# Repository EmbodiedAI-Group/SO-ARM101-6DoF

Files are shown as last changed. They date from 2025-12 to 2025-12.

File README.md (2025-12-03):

<div align="center">

   <h1>Standard Open SO-100 & SO-101 & SO-101-6DOF Arms</h1>
   <div style="display: flex; gap: 1rem; justify-content: center; align-items: center;" >
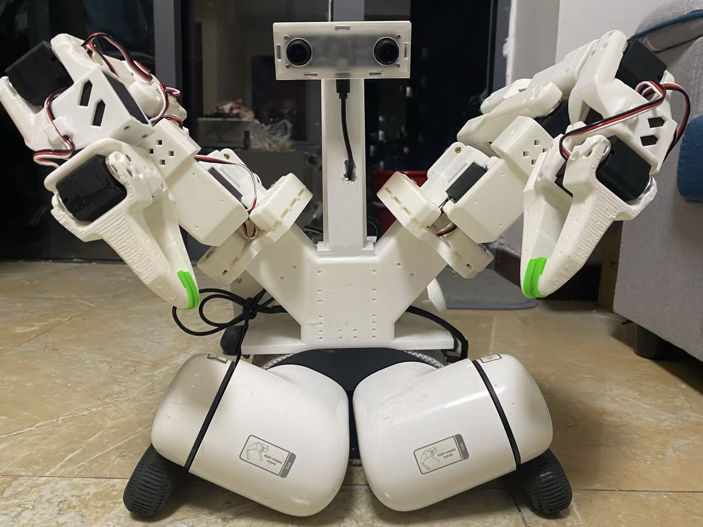
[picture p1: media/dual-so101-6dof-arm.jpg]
Dual SO-101 6dof follower arm DUAL SO-101 6DOF follower arm
   
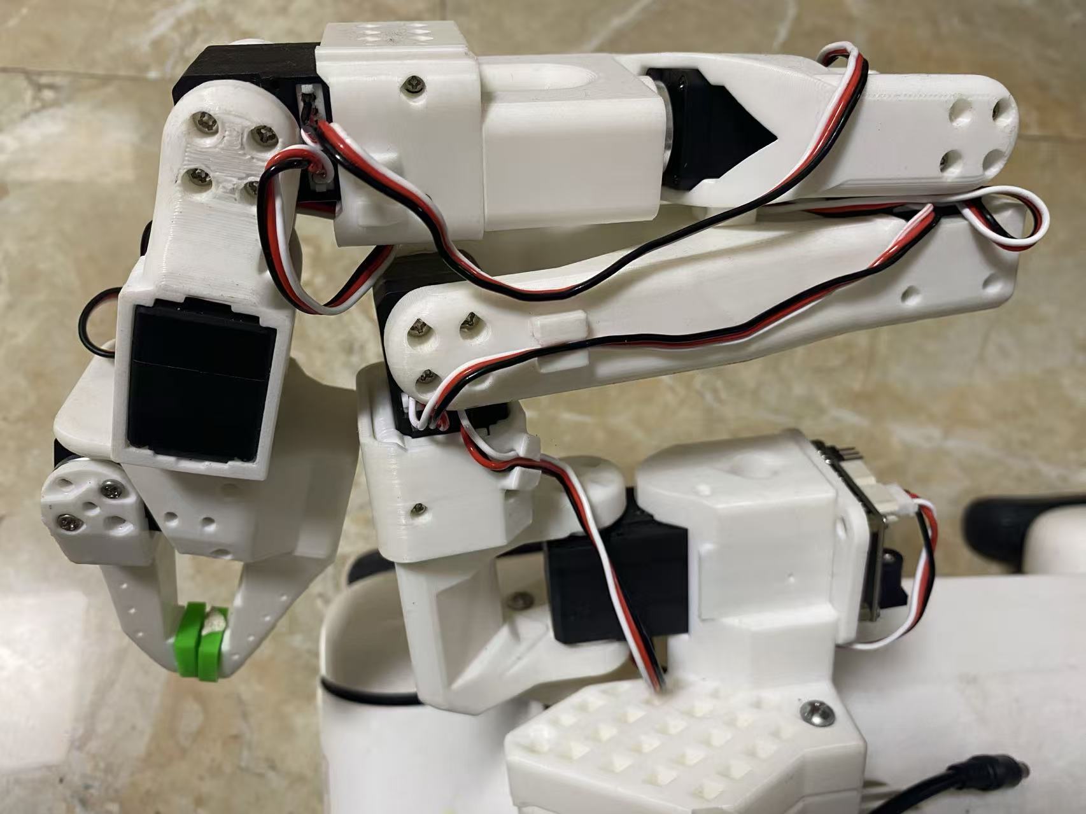
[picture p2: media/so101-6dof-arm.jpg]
SO-101 6dof follower arm SO-101 6DOF follower arm
   
   SO-101 follower arm
   SO-101 leader arm
</div>

<h2>
    <p>Build Your Own SO-101(-6DOF) Robot!</p>
</h2>

The SO‑101(-6DOF) is the next‑generation version of the SO‑100 robot arm, originally designed by the [RobotStudio](https://www.therobotstudio.com) in collaboration with [Hugging Face](https://huggingface.co/lerobot). It has improved wiring, is easier to assemble (no gear removal) and uses updated motors for the leader arm.

These arms are designed to work seamlessly with the open‑source 🤗 LeRobot library. Join our community on [Discord](https://discord.gg/ggrqhPTsMe) to collaborate on both hardware and software, and help make end‑to‑end AI for robotics more accessible.

</div>

### Documentation 📖
- For the SO‑101 docs, follow this page further.
- Here you can find the [SO‑100 docs](SO100.md) which is deprecated.

### Getting Your Own SO‑101 
You have two options:
- **Build it Yourself**
   - Source the components from the [Bill of Materials](#sourcing-parts).
   - 3D print the parts (or order the 3D printed parts), explained in [Printing the Parts](#printing-the-parts).
   - Follow our [Assembly Guide](https://huggingface.co/docs/lerobot/so101).
- **Buy a Kit**
   - Buy assembled arms or a parts kit from one of the vendors [here](#kits).
   - Optionally follow our [Assembly Guide](https://huggingface.co/docs/lerobot/so101).

### Setup with LeRobot 🤗
After sourcing all parts you can setup your SO-101(-6DOF) with LeRobot [tutorial](https://huggingface.co/docs/lerobot/so101). 

### Optional Hardware 🔧
This repository also includes a range of optional hardware designs such as a raised leader base and different camera mounts. Here you can explore the [full list](#optional-hardware).

## Kits

You can find all optional for SO-100/SO-101 kits here:

- from PartaBot :us: [US](https://partabot.com) (They include **assembled** versions, and also sell LeKiwi and Koch robots)
- from Seeed studio :earth_africa: [International](https://www.seeedstudio.com/SO-ARM100-Low-Cost-AI-Arm-Kit.html) or :cn: [China](https://item.taobao.com/item.htm?id=878010637397&skuId=5915703371829&spm=a213gs.v2success.0.0.4cbf4831mkqWLn) or :jp: [Akizuki Denshi](https://akizukidenshi.com/catalog/g/g131169/) or [Aliexpress](https://www.aliexpress.com/item/3256808696884714.html?gatewayAdapt=4itemAdapt) (They include **3d printed kits**)
- from WowRobo :earth_africa: [International](https://shop.wowrobo.com/products/so-arm101-diy-kit-assembled-version-1) or :cn: [China](https://item.taobao.com/item.htm?ft=t&id=860171734711) (They include **assembled** versions)
- from Sudoremove :kr: [South Korea](https://smartstore.naver.com/sudoremove/products/12022333117)
- from NeoBot :cn: [China](https://item.taobao.com/item.htm?ft=t&id=957685951340)

Additionally you can find SO-100 follower arm kit (without leader arm) on [Phospho](https://robots.phospho.ai). It can be especially useful if you own a VR headset.

## Sourcing Parts

The follower and leader arm for this teleoperation setup will almost the same off the shelf parts (except for the motors). If you plan on creating the classic teleoperation set up to be used with the `LeRobot` library please buy from the Parts for Two Arms below. 

We only have links for US, EU, CN, and JP for now. If you find links for other countries, please create an issue or PR so that we add them to the list. Note that prices and items may vary depending on geographic location.

> [!IMPORTANT]  
> The STS3215 motors for the follower arm comes in two sizes. The 7.4V has a stall torque of 16.5kg.cm at 6V (and likely slightly less for a 5V power supply). The 12V version has a stall torque of 30kg.cm. While we found the 7.4V to be sufficient, if you would like more powerful motors you can buy the 12V version [here](https://www.alibaba.com/product-detail/6PCS-12V-30KG-STS3215-High-Torque_1601216757543.html). Note if you do this, you will also have to buy a 12V 5A+ power supply instead of a 5V one. The leader arm is always 7.4V for the SO101.

#### Parts For Two Arms (Follower and Leader Setup):

| Part | Amount | Unit Cost (US) | Buy US | Unit Cost (EU) | Buy EU | Unit Cost (RMB) | Buy CN | Unit Cost (JPY) | Buy JP |
| --- | --- | --- | --- | --- | --- | --- | --- | --- | --- |
| STS3215 Servo 7.4V, 1/345 gear (C001) **<sup>[2](#leaderbundle)</sup>  | 7 | $13.89 | [Alibaba](https://www.alibaba.com/product-detail/Top-Seller-Low-Cost-Feetech-STS3215_1600999461525.html) | €12.2 | [Alibaba](https://www.alibaba.com/product-detail/Top-Seller-Low-Cost-Feetech-STS3215_1600999461525.html) | ￥97.72 | [TaoBao](https://item.taobao.com/item.htm?id=712179366565&skuId=5268252241438)  | ￥2,980 | [Akizuki Denshi](https://akizukidenshi.com/catalog/g/g116312/)  |
| STS3215 Servo 7.4V, 1/191 gear (C044) **<sup>[2](#leaderbundle)</sup> | 2 | $13.89 | [Alibaba](https://www.alibaba.com/product-detail/Feetech-STS3215-SO-ARM101-Servo-7_1601430747897.html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) | €12.2 | [Alibaba](https://www.alibaba.com/product-detail/Feetech-STS3215-SO-ARM101-Servo-7_1601430747897.html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) | ￥97.72 | -  | ￥2,980 | [Akizuki Denshi](https://akizukidenshi.com/catalog/g/g131131/)  |
| STS3215 Servo 7.4V, 1/147 gear (C046) **<sup>[2](#leaderbundle)</sup> | 3 | $13.89 | [Alibaba](https://www.alibaba.com/product-detail/Feetech-STS3215-SO-ARM101-Servo-7_1601430760797.html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) | €12.2 | [Alibaba](https://www.alibaba.com/product-detail/Feetech-STS3215-SO-ARM101-Servo-7_1601430760797.html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) | ￥97.72 | -  | ￥2,980 | [Akizuki Denshi](https://akizukidenshi.com/catalog/g/g131132/)  |
| Motor Control Board | 2 | $10.6 | [Amazon](https://www.amazon.com/Waveshare-Integrates-Control-Circuit-Supports/dp/B0CTMM4LWK/) | €11.4 | [Amazon](https://www.amazon.fr/-/en/dp/B0CJ6TP3TP/) | ￥27 | [TaoBao](https://detail.tmall.com/item.htm?id=738817173460&skuId=5096283384143) | ￥980 | [Akizuki Denshi](https://akizukidenshi.com/catalog/g/g131227/)  |
| USB-C Cable 2 pcs | 1 | $7 | [Amazon](https://www.amazon.com/Charging-etguuds-Charger-Braided-Compatible/dp/B0B8NWLLW2/?th=1) | €7 | [Amazon](https://www.amazon.fr/dp/B07BNF842T/) | ￥23.9\*2 | [TaoBao](https://detail.tmall.com/item.htm?id=44425281296&skuId=5611379016222)  | ￥1,498 | [Amazon](https://www.amazon.co.jp/dp/B0C3H9L6KZ)  |
| Power Supply | 2 | $10 | [Amazon](https://www.amazon.com/Facmogu-Switching-Transformer-Compatible-5-5x2-1mm/dp/B087LY41PV/) | €15.7 | [Amazon](https://www.amazon.fr/-/en/dp/B01HRR9GY4/) | ￥22.31 | [TaoBao](https://item.taobao.com/item.htm?id=544824248494&skuId=4974994129990)  | ￥1,550 | [Akizuki Denshi](https://akizukidenshi.com/catalog/g/g106238/)  |
| Table Clamp 4pcs | 1 | $9 | [Amazon](https://www.amazon.com/TAODAN-Trigger-Ratchet-Woodworking-Processes/dp/B0DJNXF8WH?rps=1&sr=1-18) | €9.7 | [Amazon](https://www.amazon.fr/Connex-COXT865210-Lot-Serre-joints-bricolage/dp/B00NA3T2CQ) | ￥5.2*4 | [TaoBao](https://detail.tmall.com/item.htm?id=801399113134&skuId=5633627126649) | ￥2,200 | [Amazon](https://www.amazon.co.jp/dp/B0DJNXF8WH)  |
| Screwdriver Set<sup>[1](#myfootnote1)</sup> | 1 | $6 | [Amazon](https://www.amazon.com/Precision-Phillips-Screwdriver-Electronics-Computer/dp/B0DB227RTH) | €9 | [Amazon](https://www.amazon.fr/Vinabo-Magnétique-Electronique-Réparation-Informatique/dp/B0BNQBNFFJ) | ￥14.9 | [TaoBao](https://detail.tmall.com/item.htm?id=675684600845&skuId=4856851392176) | ￥500 | [Amazon](https://www.amazon.co.jp/dp/B01MDNJVMN)  |
| Total | --- | $229.88 | --- | €226.3 | --- | ￥1343.16 | --- | ￥44,530 | --- |

<a name="leaderbundle">2</a>: You can buy **all six STS3215 servos needed for the SO-101 leader arm**  
(3 × 1/147 gear (C046), 2 × 1/191 gear (C044), 1 × 1/345 gear (C001)) in a single bundle on [Alibaba](https://www.alibaba.com/product-detail/6PCS-7-4V-STS3215-Servos-for_1601428584027.html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).

#### Parts for One Follower Arm:

| Part | Amount | Unit Cost (US) | Buy US | Unit Cost (EU) | Buy EU | Unit Cost (RMB) | Buy CN | Unit Cost (JPY) | Buy JP |
| --- | --- | --- | --- | --- | --- | --- | --- | --- | --- |
| STS3215 Servo 7.4V, 1/345 gear (C001) | 6 | $13.89 | [Alibaba](https://www.alibaba.com/product-detail/Top-Seller-Low-Cost-Feetech-STS3215_1600999461525.html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) | €12.2 | [Alibaba](https://www.alibaba.com/product-detail/Top-Seller-Low-Cost-Feetech-STS3215_1600999461525.html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) | ￥97.72 | [TaoBao](https://item.taobao.com/item.htm?id=712179366565&skuId=5268252241438)  | ￥2,980 | [Akizuki Denshi](https://akizukidenshi.com/catalog/g/g116312/)  |
| Motor Control Board | 1 | $10.6 | [Amazon](https://www.amazon.com/Waveshare-Integrates-Control-Circuit-Supports/dp/B0CTMM4LWK/) | €11.4 | [Amazon](https://www.amazon.fr/-/en/dp/B0CJ6TP3TP/) | ￥27 | [TaoBao](https://detail.tmall.com/item.htm?id=738817173460&skuId=5096283384143) | ￥980 | [Akizuki Denshi](https://akizukidenshi.com/catalog/g/g131227/)  |
| USB-C Cable 2 pcs | 1 | $7 | [Amazon](https://www.amazon.com/Charging-etguuds-Charger-Braided-Compatible/dp/B0B8NWLLW2/?th=1) | €7 | [Amazon](https://www.amazon.fr/dp/B07BNF842T/) | ￥23.9 | [TaoBao](https://detail.tmall.com/item.htm?id=44425281296&skuId=5611379016222)  | ￥1,498 | [Amazon](https://www.amazon.co.jp/dp/B0C3H9L6KZ)  |
| Power Supply | 1 | $10 | [Amazon](https://www.amazon.com/Facmogu-Switching-Transformer-Compatible-5-5x2-1mm/dp/B087LY41PV/) | €15.7 | [Amazon](https://www.amazon.fr/-/en/dp/B01HRR9GY4/) | ￥22.31 | [TaoBao](https://item.taobao.com/item.htm?id=544824248494&skuId=4974994129990)  | ￥1,550 | [Akizuki Denshi](https://akizukidenshi.com/catalog/g/g106238/)  |
| Table Clamp 2pcs | 1 | $5 | [Amazon](https://www.amazon.com/Mr-Pen-Carpenter-Clamp-6inch/dp/B092L925J4/) | €8 | [Amazon](https://www.amazon.fr/-/en/dp/B08HZ1QRBF/) | ￥7.8 | [TaoBao](https://detail.tmall.com/item.htm?id=738636473238&skuId=5505939904942) | ￥2,200 | [Amazon](https://www.amazon.co.jp/dp/B0DJNXF8WH)  |
| Screwdriver Set<sup>[1](#myfootnote1)</sup> | 1 | $6 | [Amazon](https://www.amazon.com/Precision-Phillips-Screwdriver-Electronics-Computer/dp/B0DB227RTH) | €9 | [Amazon](https://www.amazon.fr/Vinabo-Magnétique-Electronique-Réparation-Informatique/dp/B0BNQBNFFJ) | ￥14.9 | [TaoBao](https://detail.tmall.com/item.htm?id=675684600845&skuId=4856851392176) | ￥500 | [Amazon](https://www.amazon.co.jp/dp/B01MDNJVMN)  |
| Total | --- | $121.94 | --- | €124.3 | --- | ￥682.23 | --- | ￥24,414 | --- |

<a name="myfootnote1">1</a>: You do not need to use this exact screwdriver set, but it is highly recommended to have phillips head screw driver sizes #0 and #1 for easiest screw installation and removal. These are both standard sizes which will likely appear in most small screwdriver sets.

## Printing the Parts

A variety of 3D printers are acceptable to print the parts necessary of the follower and leader arm. Follow the steps below to ensure a good print.

### Step 1: Choose a Printer
The STL files provided are ready to print on many FDM printers. Below are the tested and suggested settings though others may work.
   1. Material: PLA+
   2. Nozzle Diameter and Precision: 0.4mm nozzle diameter at 0.2mm layer height or 0.6mm nozzle at 0.4mm layer height.
   3. Infill Density: 15%
   4. Sample Printers: [Prusa MINI+](https://www.prusa3d.com/product/original-prusa-mini-semi-assembled-3d-printer-4/), [UP Plus 2](https://shop.tiertime.com/product/tiertime-up-plus-2-3d-printer/), [Creality Ender 3](https://www.amazon.com/Comgrow-Creality-Ender-Aluminum-220x220x250mm/dp/B07BR3F9N6/), [Bambu Lab A/P/X-series](https://bambulab.com)

### Step 2: Set up the Printer
   1. Ensure that the printer is calibrated and the bed level is correctly set using the printer specific instructions.
   2. Clean the print bed, making sure it is free from dust, or grease. If cleaning the bed using water, or other liquid, dry the bed.
   3. If your printer recommends it, use a standard glue stick and apply a thin, even layer of glue across the print area of the bed. Avoid clumping or uneven application.
   4. Load the printer filament using printer specific instructions.
   5. Ensure the printer settings match the ones suggested above (most printers have multiple settings so choose the ones that most closely match).
   6. Set for supports everywhere but ignore slopes greater than 45 degrees to the horizontal.
   7. There should be no supports in the screw holes with horizontal axes.
### Step 3: Check Printer Accuracy
   1. In the [Gauges](STL/Gauges) folder, there are two types of gauges, one to check the size of print against a standard 4x2 lego block and one against a STS3215 servo.
      1. If you have a STS3215 servo, print:
         1. [Gauge Zero](STL/Gauges/Gauge_0.STL)
         2. [Gauge Tight](STL/Gauges/Gauge_tight_1.STL)
      2. If you have a standard lego block, print:
         1. [Gauge Zero](STL/Gauges/Lego_Size_Test_02_zero.STL)
         2. [Gauge -0.1](STL/Gauges/Lego_Size_Test_02_minuspoint1.STL)
   2. Test the gauge 0 against your given object (Lego or Servo). The fit should be similar to this [tutorial](https://youtu.be/dss8E3DG2rA).
   3. If the fit is appropriate, go onto Step 4, otherwise, change your printer settings and try again or create an issue.
### Step 4: Print the Parts
All the parts for the leader or follower are for easy 3D printing already contained in a **single file**, correctly orientated for z upwards to minimize supports.
   1. For printer bed sizes of 220mmx220mm (such as the Ender), print these files:
      - [Follower](STL/SO101/Follower/Ender_Follower_SO101.stl)
      - [Leader](STL/SO101/Leader/Ender_Leader_SO101.stl)
   2. For printer bed sizes of 205mm x 250mm (such as the Prusa/Up):
      1. [Follower](STL/SO101/Follower/Prusa_Follower_SO101.stl)
      2. [Leader](STL/SO101/Leader/Prusa_Leader_SO101.stl)

This table contains all individual files:
<details>
<summary>Individual Part Files</summary>

#### Common Parts

| Part | Link |
|---|---|
| Base_motor_holder_SO101.stl | [Base_motor_holder_SO101.stl](STL/SO101/Individual/Base_motor_holder_SO101.stl) |
| Base_SO101.stl | [Base_SO101.stl](STL/SO101/Individual/Base_SO101.stl) |
| Motor_holder_SO101_Base.stl | [Motor_holder_SO101_Base.stl](STL/SO101/Individual/Motor_holder_SO101_Base.stl) |
| Motor_holder_SO101_Wrist.stl | [Motor_holder_SO101_Wrist.stl](STL/SO101/Individual/Motor_holder_SO101_Wrist.stl) |
| Under_arm_SO101.stl | [Under_arm_SO101.stl](STL/SO101/Individual/Under_arm_SO101.stl) |
| Upper_arm_SO101.stl | [Upper_arm_SO101.stl](STL/SO101/Individual/Upper_arm_SO101.stl) |
| Rotation_Pitch_SO101.stl | [Rotation_Pitch_SO101.stl](STL/SO101/Individual/Rotation_Pitch_SO101.stl) |
| Wrist_Roll_Pitch_SO101.stl | [Wrist_Roll_Pitch_SO101.stl](STL/SO101/Individual/Wrist_Roll_Pitch_SO101.stl) |
| WaveShare_Mounting_Plate_SO101.stl  | [WaveShare_Mounting_Plate_SO101.stl](STL/SO101/Individual/WaveShare_Mounting_Plate_SO101.stl) |

#### Leader‑Specific Parts

| Part | Link |
|---|---|
| Handle_SO101.stl | [Handle_SO101.stl](STL/SO101/Individual/Handle_SO101.stl) |
| Trigger_SO101.stl | [Trigger_SO101.stl](STL/SO101/Individual/Trigger_SO101.stl) |
| Wrist_Roll_SO101.stl  | [Wrist_Roll_SO101.stl](STL/SO101/Individual/Wrist_Roll_SO101.stl) |

#### Follower‑Specific Parts

| Part | Link |
|---|---|
| Moving_Jaw_SO101.stl | [Moving_Jaw_SO101.stl](STL/SO101/Individual/Moving_Jaw_SO101.stl) |
| Wrist_Roll_Follower_SO101.stl | [Wrist_Roll_Follower_SO101.stl](STL/SO101/Individual/Wrist_Roll_Follower_SO101.stl) |
</details>

### Step 5: Remove Supports
   1. After the print is done, use a putty knife to scrape the the parts off the print bed.
   2. Remove any support material from parts.

### Don't Own a 3D printer?
Go here: [Printing services](./3DPRINT.md)

## Optional Hardware
<!--Note: no hardware emoji here so links work correctly-->
Extend your SO‑100/SO‑101 with these add-ons.
<details>
<summary>Add‑ons</summary>

#### 0. XLeRobot

A dual-arm mobile robot for daily use, with 2x SO101 arms, 1x Lekiwi base, 1x 300Wh Anker Battery, 2x wrist RGB cameras, 1x head depth camera (with a 2-dof neck). Total cost 660$.

82c2b72eab7c716b90fafac0a9caf895

[→ Full Documentation](https://xlerobot.readthedocs.io/en/latest/index.html), with detailed BOM, 3D printing models, assembly guide, simulation, and teleop guide.

#### 1. Mount Helper  
Print the handy mount jig for easier alignment during assembly.  

[→ View README](Optional/Mount_Helper/README.md)

Mount Helper

#### 2. Overhead Camera Mount 

For bird’s‑eye views in single or bi‑manual setups.  
(SO100/101)

| Webcam  | 32×32 Cam Module |
|:---:|:---:|
 |  
| [Instructions](Optional/Overhead_Cam_Mount_Webcam/README.md) | [Instructions](Optional/Overhead_Cam_Mount_32x32_UVC_Module/README.md) 

#### 3. Base Mounts

| Raised Leader Base | 4040 Aluminum Profile Mount |
|:---:|:---:|
 |   
[Download STL](Optional/Raised_Base/Raised_Base_Extension.stl) | [Instructions](Optional/4040_Base_Mount/README.md)

#### 4. Tactile Sensing (AnySkin)  
Add touch sensing to your gripper.  

[→ Find on WOWROBO](https://shop.wowrobo.com/products/enhanced-anyskin-premium-crafted-editionwowskin)

AnySkin Sensor

#### 5. Wrist‑Mount Cameras

| 32×32 UVC Hex Nut (SO101) | 32×32 UVC Integrated (SO100/101) | 32×32 UVC Plug‑on | RealSense D405 | RealSense D435/D435I | Webcam (Vinmooog) |
| --- | --- | --- | --- | --- | --- |
|  |  |  |  |  |  |
| [Instructions](Optional/SO101_Wrist_Cam_Hex-Nut_Mount_32x32_UVC_Module) | [Instructions](Optional/Wrist_Cam_Mount_32x32_UVC_Module/README.md) | [Instructions](Optional/Wrist_Cam_Plug_Mount_32x32_UVC_Module) | [Instructions](Optional/Wrist_Cam_Mount_RealSense_D405) | [Instructions](Optional/Wrist_Cam_Mount_RealSense_D435) | [Instructions](Optional/Wrist_Cam_Mount_Vinmooog_Webcam) |

#### 6. Compliant Gripper
Add some flexibility to your gripper by downloading the compliant gripper parts and printing them using a flexible filament like TPU 95A. 

[→ View README](Optional/Compliant_Gripper/README.md). 



#### 7. Compliant Gripper (new)
Printed with TPU 95A for the finger and PLA for the base. 
Better structure and better grasp (both precision and power). No need to print support for the TPU finger. Requires 2 additional M3 screws, optional 3M gripper tape for higher friction.
d2e57534a9e55a3d4dc0d644242cd044

[→ Find on XLeRobot](https://github.com/Vector-Wangel/XLeRobot/tree/main/hardware)
</details>

## Debugging Motors
For debugging, any Windows PC can connect over USB to program the servos and to debug or do tests. To do so download [Feetech Software](https://www.feetechrc.com/software.html). For Ubuntu, you can use [FT_SCServo_Debug_Qt](https://github.com/Kotakku/FT_SCServo_Debug_Qt). Note: This step is not necessary as motors can be configured using the LeRobot Library, but this can be helpful for debugging.

## SO101-ARM-6DOF
  Dual SO-101 6dof follower arm DUAL SO-101 6DOF follower arm
   SO-101 6dof follower arm SO-101 6DOF follower arm

Simply but effectively, we reuse the "Wrist_Roll_Pitch_SO101" and modify the "Under_arm_SO101" to "Arm5"(In STEP/SO101-6DoF) and finally get a standard 6DoF arm as above. It becomes much more flexible but still keeps light-weight! 

## SO101-ARM-6DOF Contributors

Design: [oym](https://github.com/oym1994) [hhuysqt](https://github.com/hhuysqt)

Print:  [hhuysqt](https://github.com/hhuysqt)

## TODO For SO101-ARM-6DOF
1、 URDF from Solidworks

2、 Simulation

3、 Inverse Kinematics(IK) and Forward Kinematics(FK) with pydrake and URDF

## More
Waiting for our Lerobot-Orthrus, a very interesting dual-arm robotic dog, for domestic tasks and entertainment! 

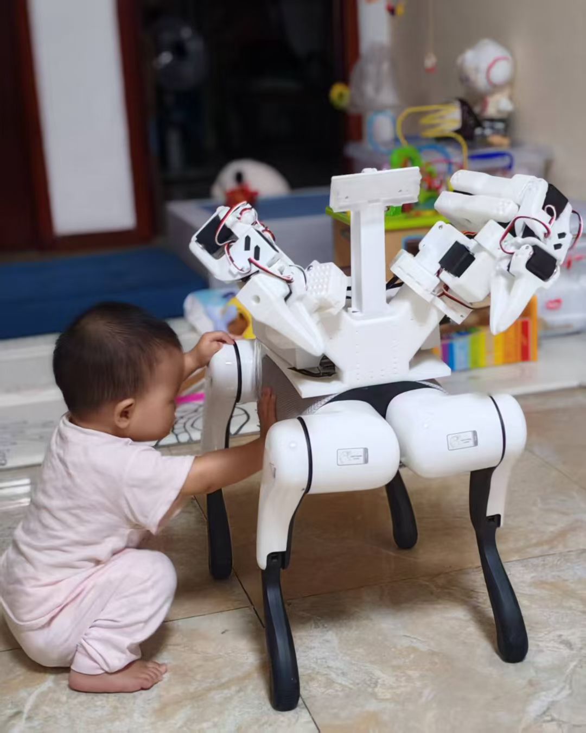
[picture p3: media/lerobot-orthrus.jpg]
Lerobot-Orthrus


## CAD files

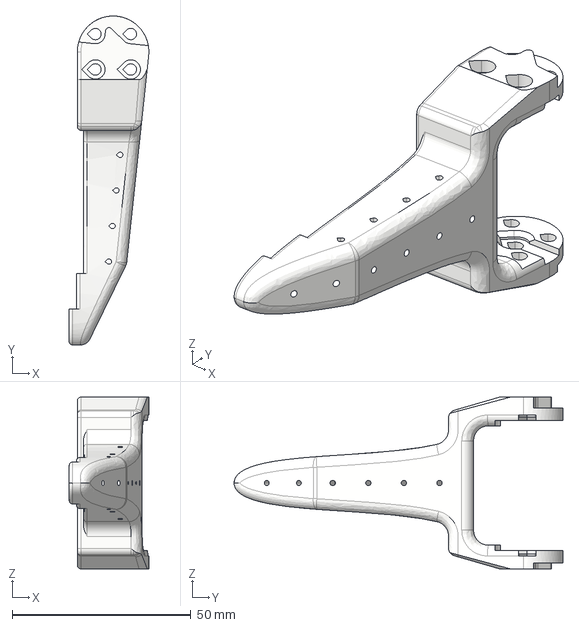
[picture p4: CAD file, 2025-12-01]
STEP/SO101-6DoF/Follower_Specific/Moving_Jaw_SO101.step
22.3 x 92.0 x 48.0 mm

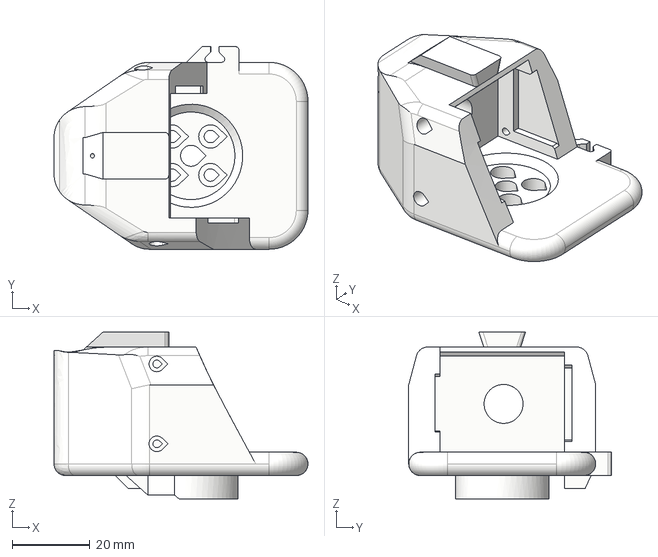
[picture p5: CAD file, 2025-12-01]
STEP/SO101-6DoF/Leader_Specific/Wrist_Roll_SO101.step
65.2 x 52.0 x 42.9 mm
Wiring_holder v1
Wiring_holder v1 (1)

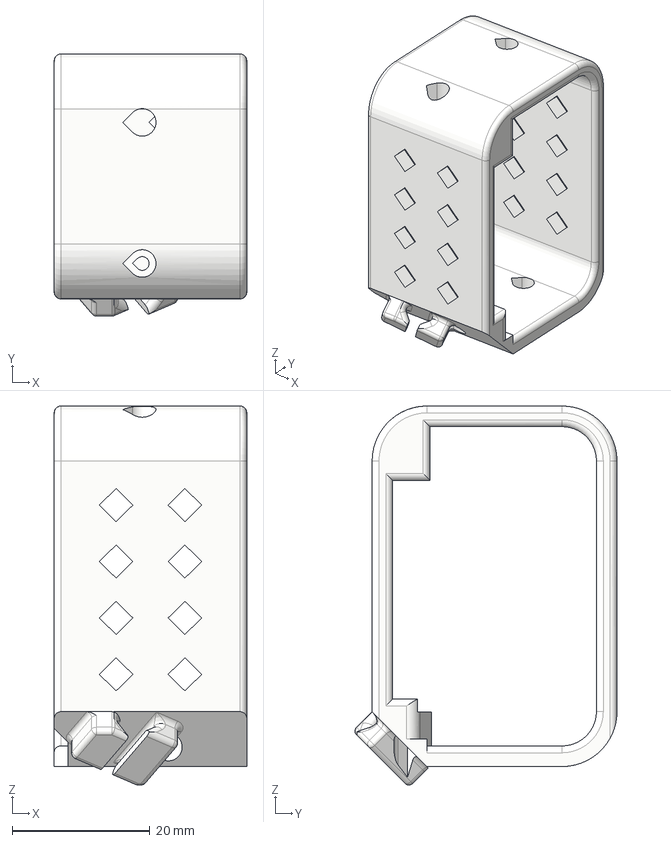
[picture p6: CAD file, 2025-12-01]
STEP/SO101-6DoF/Motor_holder_SO101_Base.step
28.0 x 38.1 x 55.1 mm
Wiring_holder v1
Wiring_holder v1 (1)
Wiring_holder v1 (2)

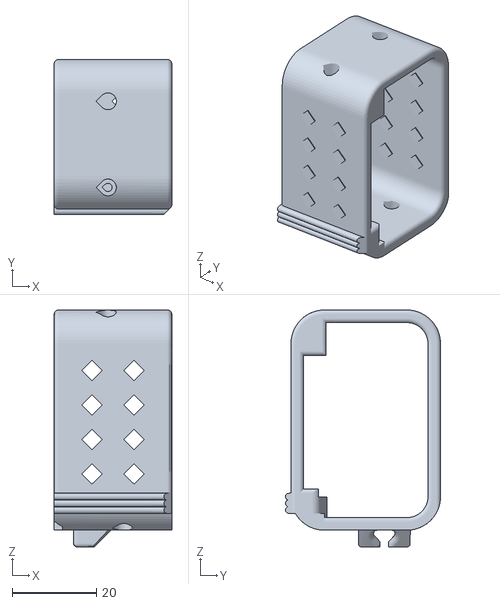
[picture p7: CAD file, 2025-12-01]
STL/SO101-6DoF/Individual/Motor_holder_SO101_Wrist.stl
28.0 x 36.9 x 56.4

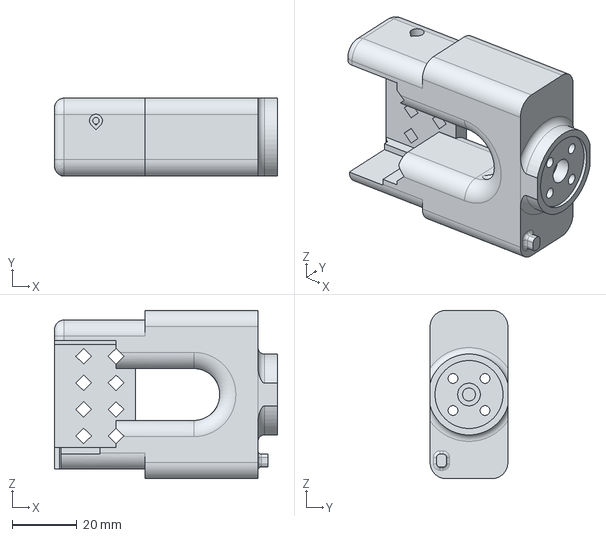
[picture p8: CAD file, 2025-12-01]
STEP/SO101-6DoF/Arm5.step
68.8 x 24.0 x 52.0 mm

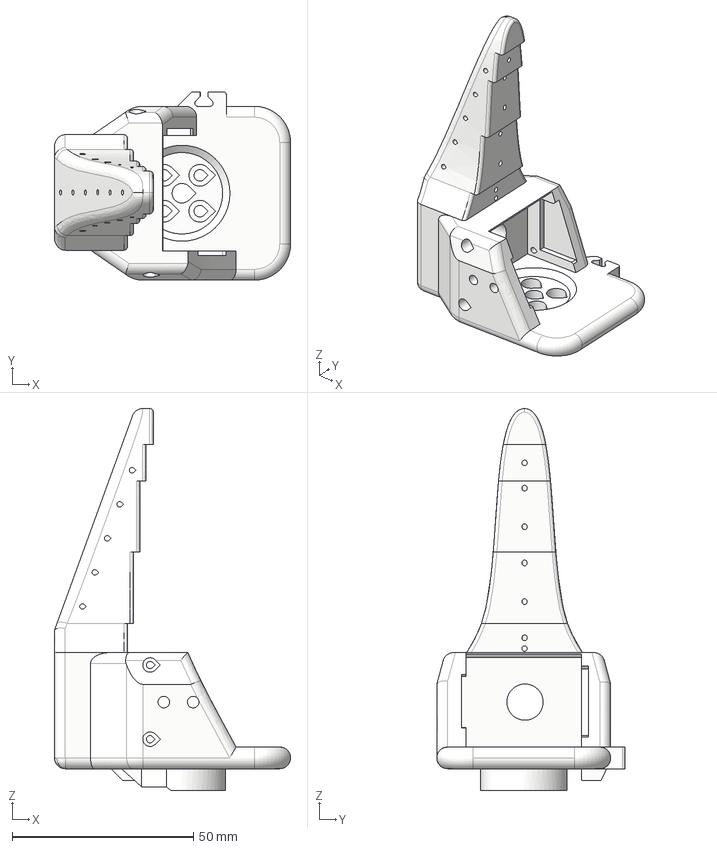
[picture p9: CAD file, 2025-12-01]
STEP/SO101-6DoF/Follower_Specific/Wrist_Roll_Follower_SO101.step
65.2 x 52.0 x 105.4 mm
Wiring_holder v1
Wiring_holder v1 (1)

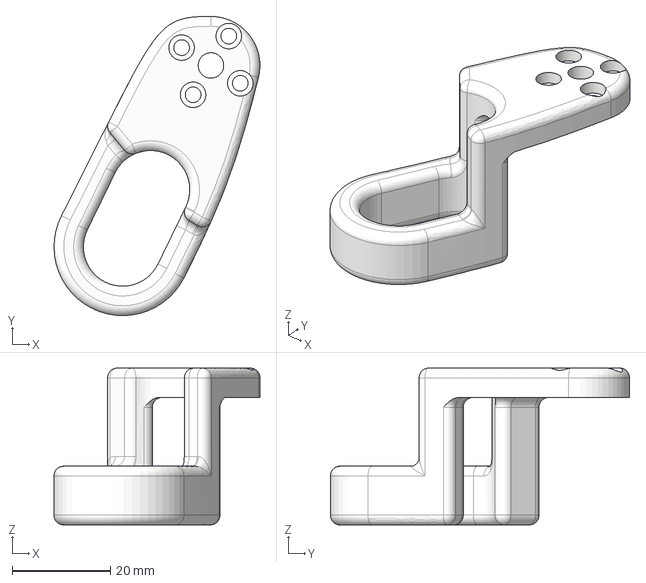
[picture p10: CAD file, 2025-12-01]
STEP/SO101-6DoF/Leader_Specific/Trigger_SO101.step
42.0 x 61.0 x 32.0 mm

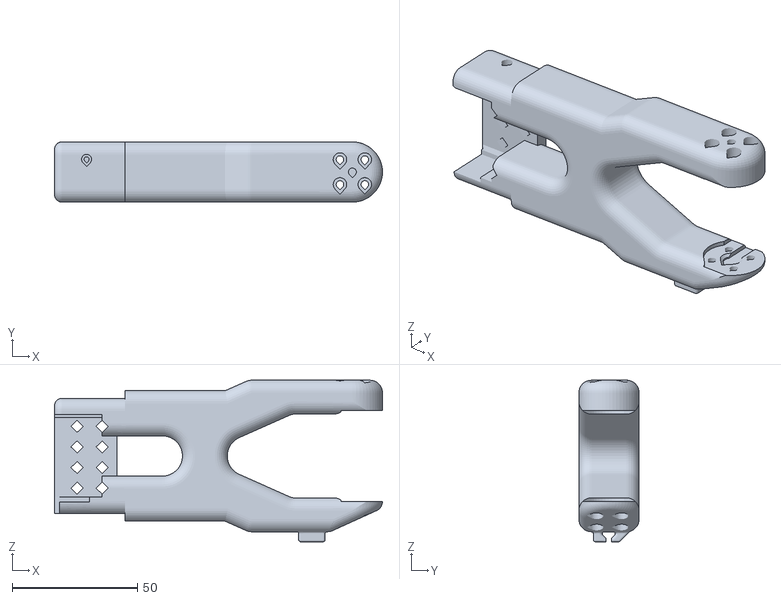
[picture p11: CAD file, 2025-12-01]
STL/SO101-6DoF/Individual/Under_arm_SO101.stl
130.7 x 24.0 x 64.4

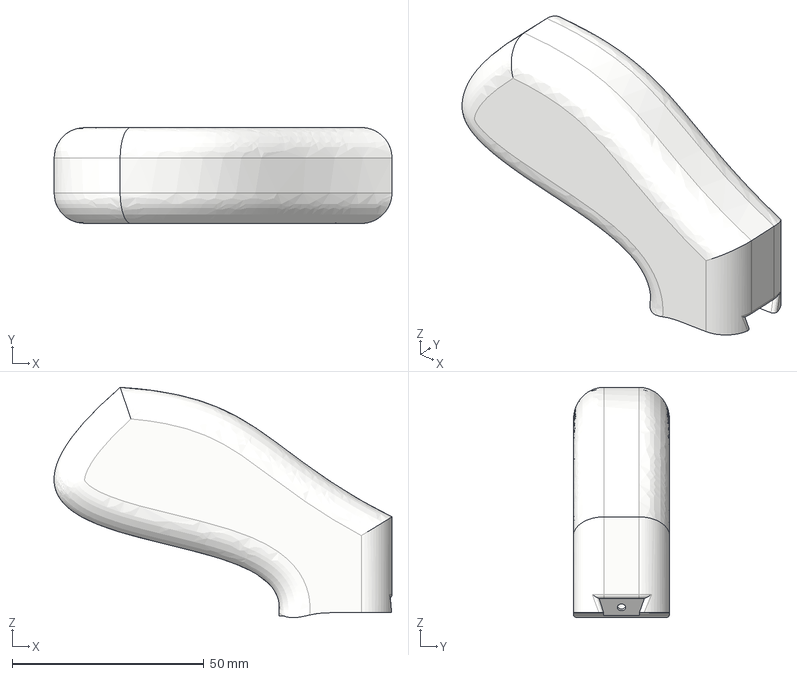
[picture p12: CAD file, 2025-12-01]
STEP/SO101-6DoF/Leader_Specific/Handle_SO101.step
88.1 x 25.0 x 60.1 mm

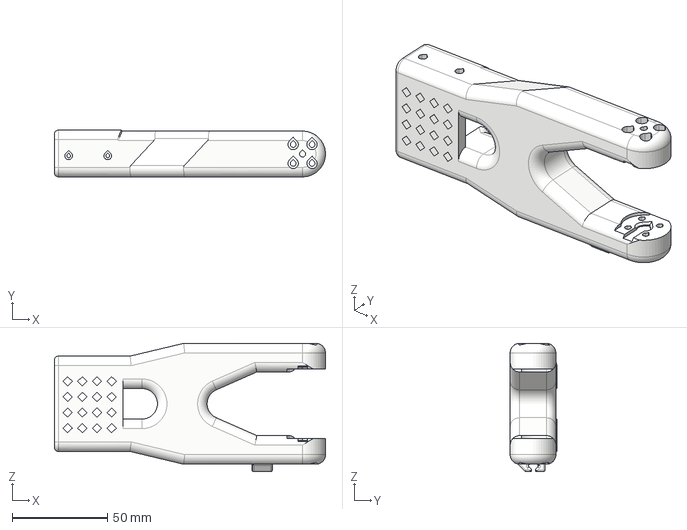
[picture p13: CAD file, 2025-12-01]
STEP/SO101-6DoF/Upper_arm_SO101.step
142.2 x 24.5 x 67.3 mm
Wiring_holder v1
Wiring_holder v1 (1)

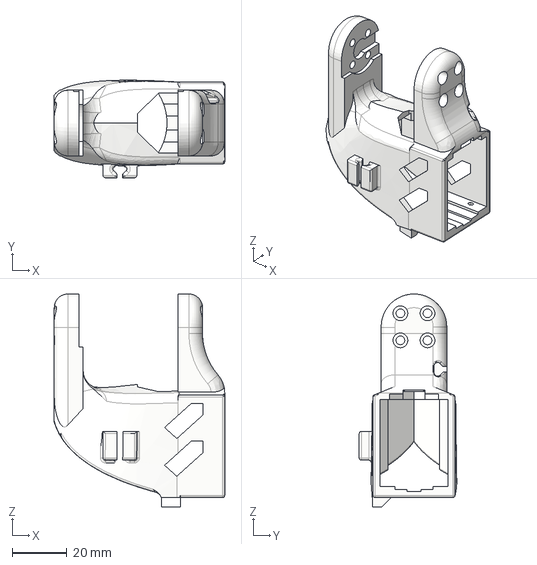
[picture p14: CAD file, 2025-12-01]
STEP/SO101-6DoF/Wrist_Roll_Pitch_SO101.step
62.3 x 35.6 x 77.8 mm

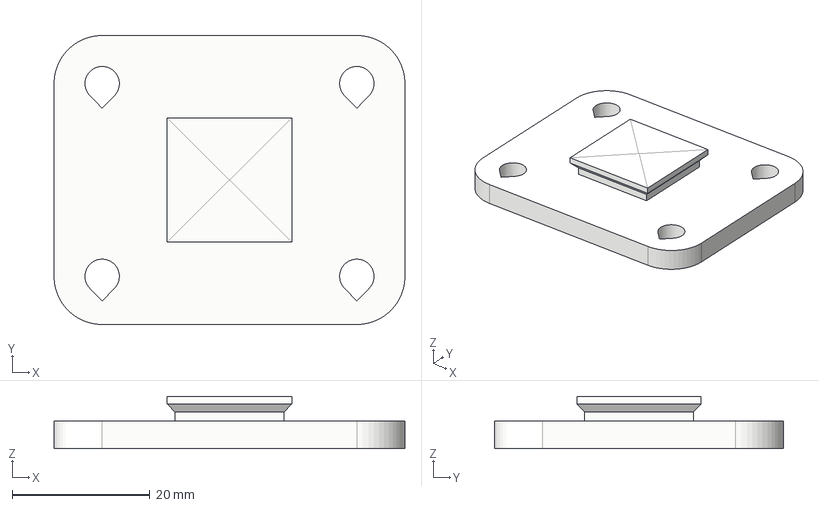
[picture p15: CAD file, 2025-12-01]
STEP/SO101-6DoF/WaveShare_Mounting_Plate_SO101.step
51.0 x 42.0 x 7.60 mm

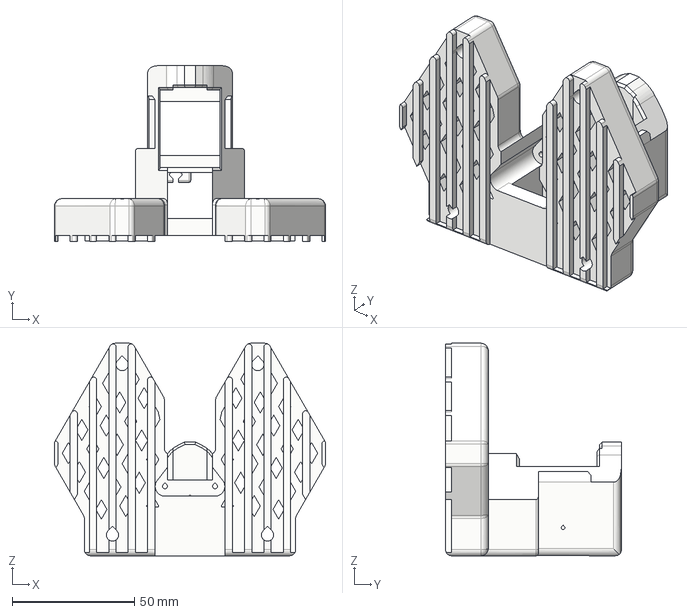
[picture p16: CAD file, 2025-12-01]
STEP/SO101-6DoF/Base_SO101.step
110.9 x 72.0 x 87.0 mm

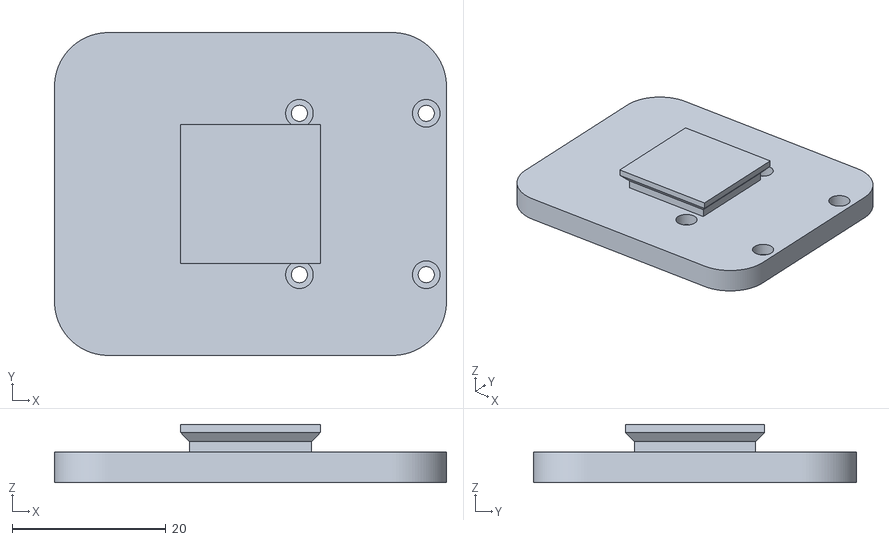
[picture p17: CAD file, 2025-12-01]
STL/SO101-6DoF/Individual/Seeedstudio_Mounting_Plate_SO101.stl
51.0 x 42.0 x 7.60

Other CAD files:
STL/SO101-6DoF/Individual/Moving_Jaw_SO101.stl
STL/SO101-6DoF/Individual/Arm5.stl
STL/SO101-6DoF/Individual/Handle_SO101.stl
STEP/SO101-6DoF/Under_arm_SO101.step
STEP/SO101-6DoF/Base_motor_holder_SO101.step
STEP/SO101-6DoF/Motor_holder_SO101_Wrist.step
STEP/SO101-6DoF/Rotation_Pitch_SO101.step
STEP/SO101-6DoF/Seeedstudio_Mounting_Plate_SO101.step
STL/SO101-6DoF/Individual/Base_SO101.stl
STL/SO101-6DoF/Individual/Base_motor_holder_SO101.stl
STL/SO101-6DoF/Individual/Motor_holder_SO101_Base.stl
STL/SO101-6DoF/Individual/Rotation_Pitch_SO101.stl
STL/SO101-6DoF/Individual/Trigger_SO101.stl
STL/SO101-6DoF/Individual/Upper_arm_SO101.stl
STL/SO101-6DoF/Individual/WaveShare_Mounting_Plate_SO101.stl
STL/SO101-6DoF/Individual/Wrist_Roll_Follower_SO101.stl
STL/SO101-6DoF/Individual/Wrist_Roll_Pitch_SO101.stl
STL/SO101-6DoF/Individual/Wrist_Roll_SO101.stl

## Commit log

2025-12-01 Add so101-6dof and update readme
    [Arm5.step, Arm5.stl, Base_SO101.step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]
2025-12-03 Clarify modification details for 6DoF arm
    Updated description of the 6DoF arm to specify 'Arm5' in the modification.
